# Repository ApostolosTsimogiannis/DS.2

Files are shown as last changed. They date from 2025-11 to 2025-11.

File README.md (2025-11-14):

# DS.2 RC Helicopter
DS.2 is a mostly printable 570 size RC helicopter for acrobatic and 3D flight.

All files are downloadable for users to build this heli. Read the manual section for a complete build instruction.
<br>

> This repository is under development. The final sections of the manual are being written and some more part files will be added.
<br>

manual

# Technical Specifications:

|Description|Value|
|---|---|
| Length | 1120mm |
| Height | 355mm |
|Width (skids)|  190mm|
|Weight (no battery)| 2180kg (1)|
|Motor Size| 4020-4025|
|Servos| Both 15mm and 20mm servos can be used|
|Main blade Size| 560-600mm (2)|
|Tail blade size| 85-95mm (2)|
|Battery|6s 4000-5600mAh|

(1) With 15mm servos

(2) Depending on tail belt length.
<br>
<br>

> ## Licensing:
> This work is licensed under Creative Commons Attribution-NonCommercial-ShareAlike 4.0 International.
To view a copy of this license, visit https://creativecommons.org/licenses/by-nc-sa/4.0/
<br>

> ## Disclaimer:
> Remote Control (RC) Helicopters can cause harm or death to people and animals and damage to property. By following the information shared in this repository, downloading the part files, and building the helicopters, or using the parts in other ways, the user agrees that all responsibility lies with them. The designer is not liable for any harm or damages arising from the use or these parts and cannot guarantee in any way the operation of the components or the helicopter as a whole. Using the parts, assembling the helicopter and using it, is at the users own risk and they hold all resposnibility and liability. Operate all RC vehicles in accordance with safety guidelines and local law requirements.
<br>

## Information/Social:
- https://www.youtube.com/@apostolosnt
- https://www.facebook.com/ds.x.rc.heli.project
- https://grabcad.com/a.t-79

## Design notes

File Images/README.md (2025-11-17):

Renders and other images of the DS.2.






1735820079988s

1744195786972s

DS 2 v2 1 front 2

DS 2 v2 1 front 3

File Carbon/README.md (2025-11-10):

All carbon parts are included in this folder.

Sheet parts are STEP files with a PDF basic drawing to ensure no issues with scaling.

The tail tube is a 25mm diameter, 680mm length tube. Tube thickness 1mm. It is strongly recommended that the inside of the carbon tube is sprayed with some varnish to stop the carbon dust from coming of with the belt.

The tail control rod is a 4mm diameter tube, 660mm length. This will be cut to size according to the type of ball links and the length of the 2.5mm thread used. See more details in the manual.

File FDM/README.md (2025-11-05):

- All parts in this folder are intended for FDM printing on your personnal 3D printer. These can be printed in SLS/MJF as well. No nested file of all parts has been created.
- Some parts e.g. canopy, are cut into appropriate sections for personal 3D printers.
- Material can be PLA, PETG or other.
- Refer to the manual section for part quantites to complete the build.

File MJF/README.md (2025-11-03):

All parts in this folder are intended for MJF printing. SLS is also suitable.

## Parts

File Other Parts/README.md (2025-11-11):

This section includes other parts that are optional. For example ESC mounting plates etc. You can choose which manufacturing method you will use for these.

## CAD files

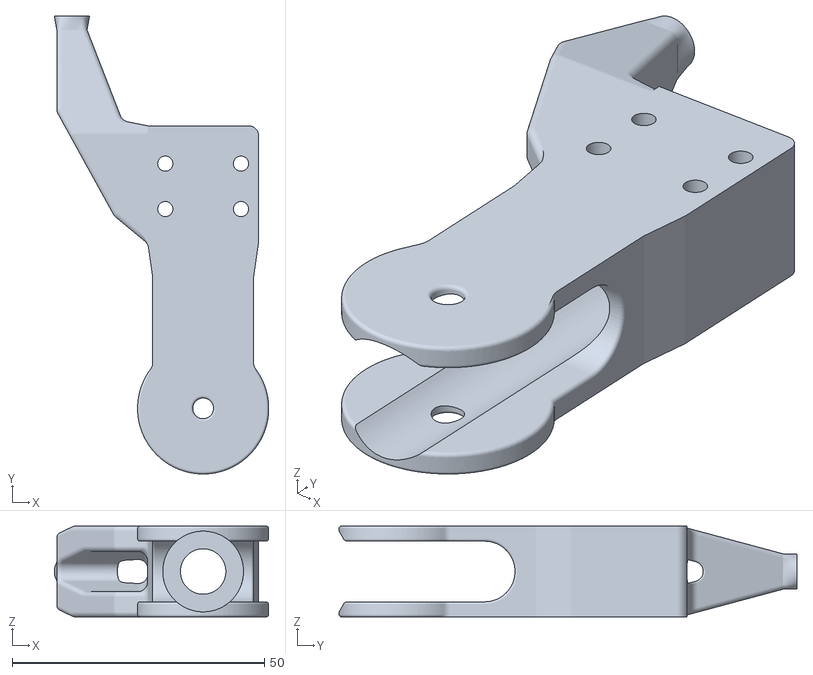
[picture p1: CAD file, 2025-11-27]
MJF/02-033-20 main grip.STL
42.5 x 90.8 x 18.0

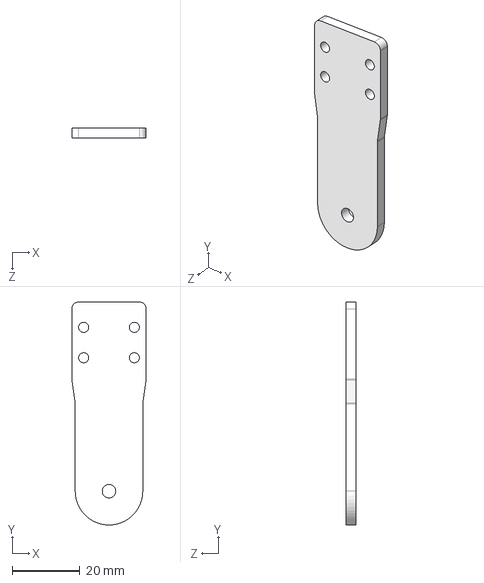
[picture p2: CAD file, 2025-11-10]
Carbon/02-014-20 main grip plate.STEP
22.0 x 66.0 x 3.00 mm

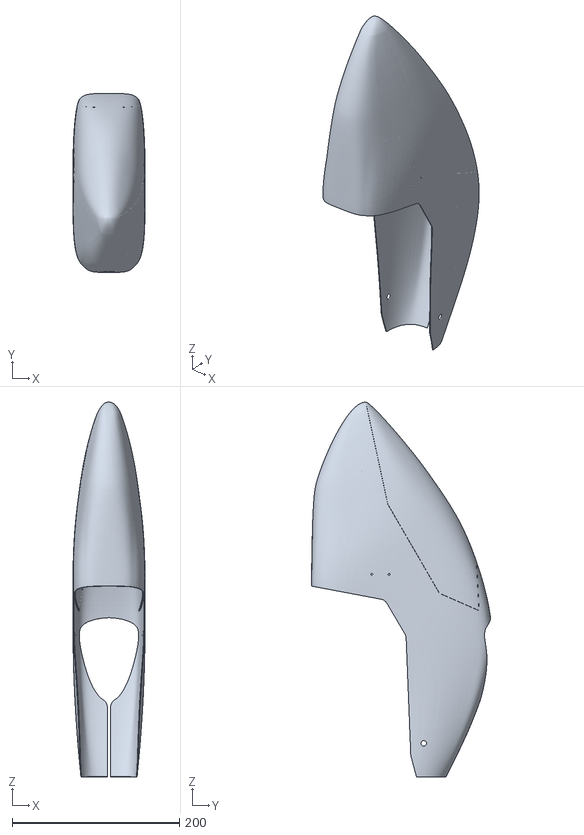
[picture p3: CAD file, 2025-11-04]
FDM/DS2 canopy assembly 0.90mm.STL
86.0 x 213.9 x 447.9

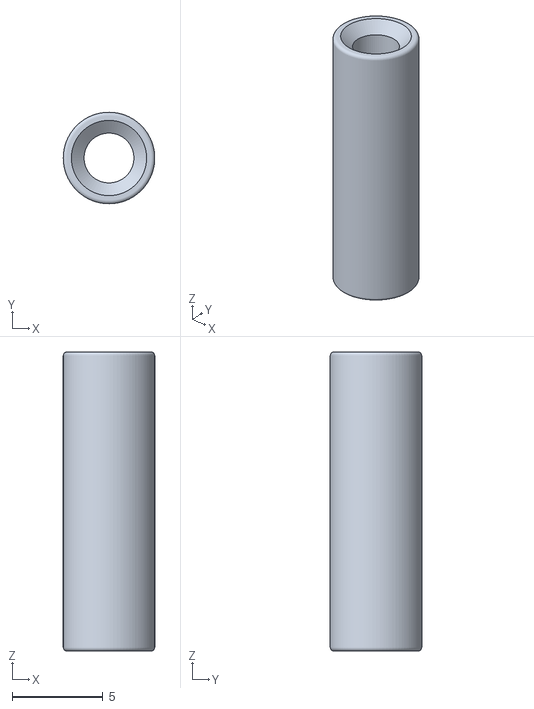
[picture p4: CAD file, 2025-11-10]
MJF/02-048-10 main grip link tube.STL
5.05 x 5.05 x 16.5

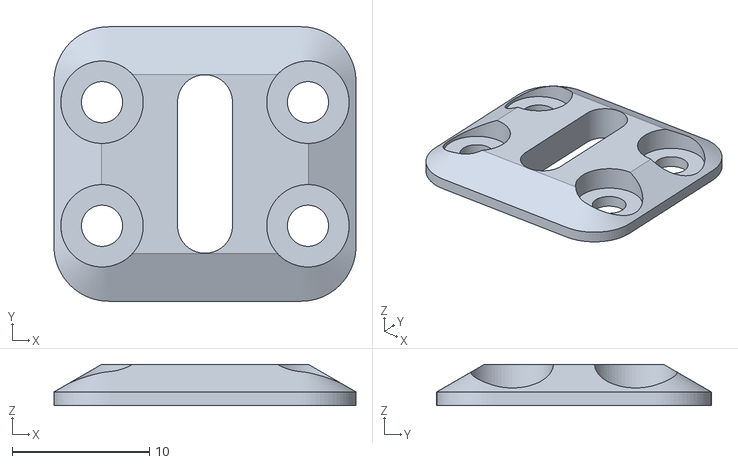
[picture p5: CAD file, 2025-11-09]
MJF/02-037-10 main grip top.STL
22.0 x 20.0 x 3.00

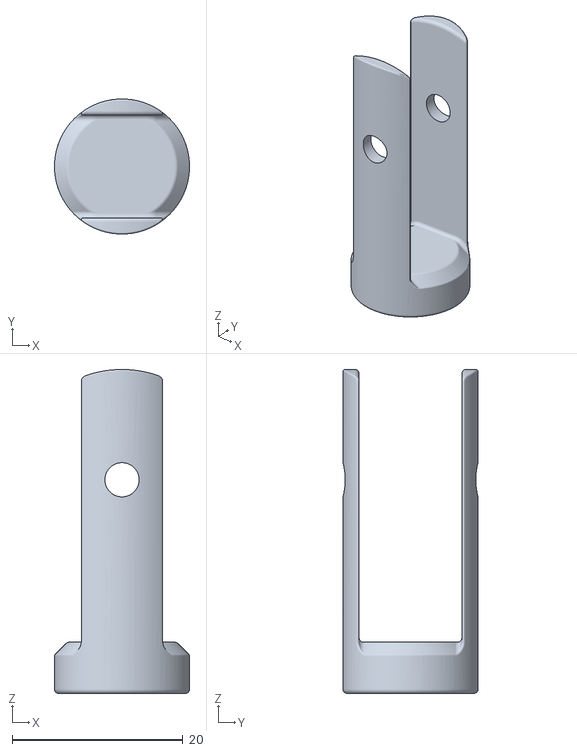
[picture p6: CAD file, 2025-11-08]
MJF/02-075-10 main grip insert.STL
15.8 x 15.8 x 37.9

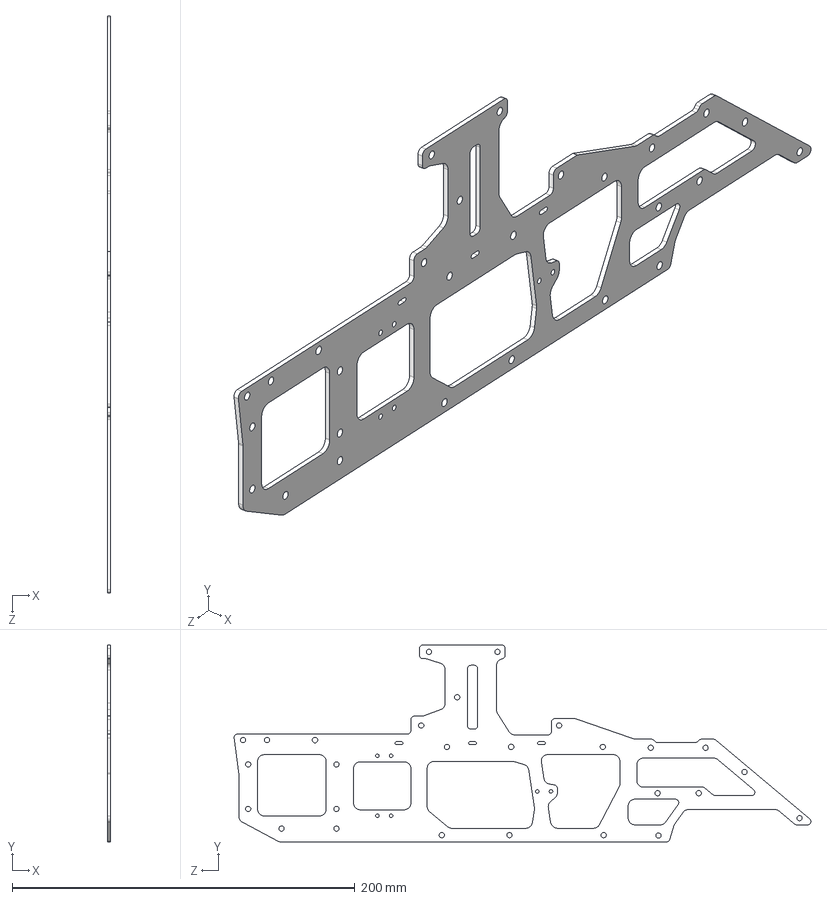
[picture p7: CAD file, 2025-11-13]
Carbon/02-010-21 side plate Right.STEP
2.00 x 115.0 x 336.7 mm

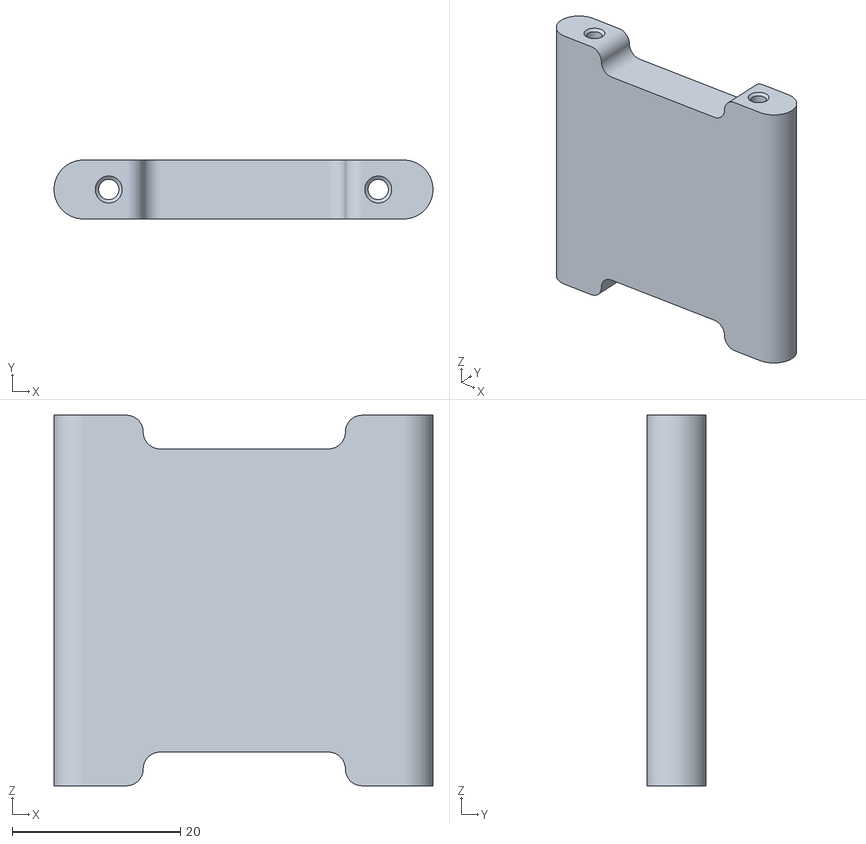
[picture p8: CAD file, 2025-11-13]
FDM/02-031-10 rear lower tray.STL
45.0 x 7.00 x 44.0

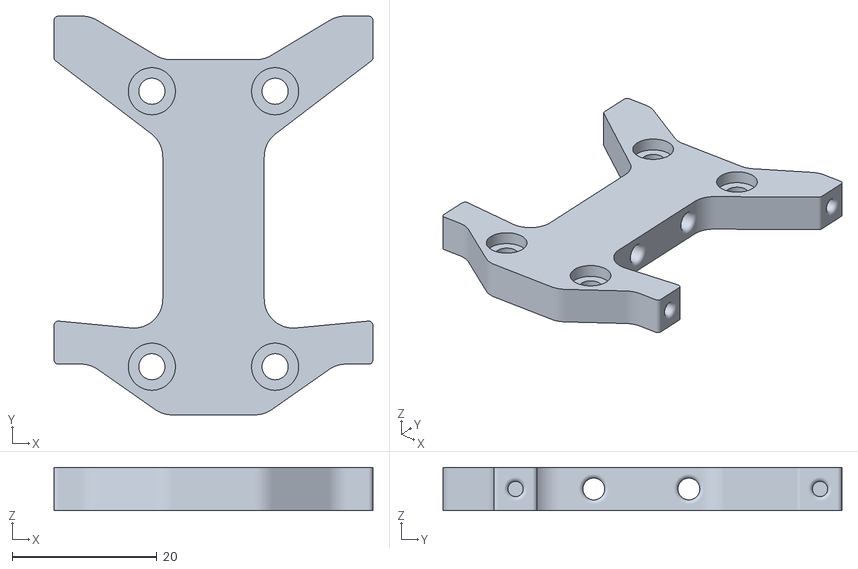
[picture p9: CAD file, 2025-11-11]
Other Parts/HW 150 mount for DS2.STL
44.0 x 55.0 x 6.00

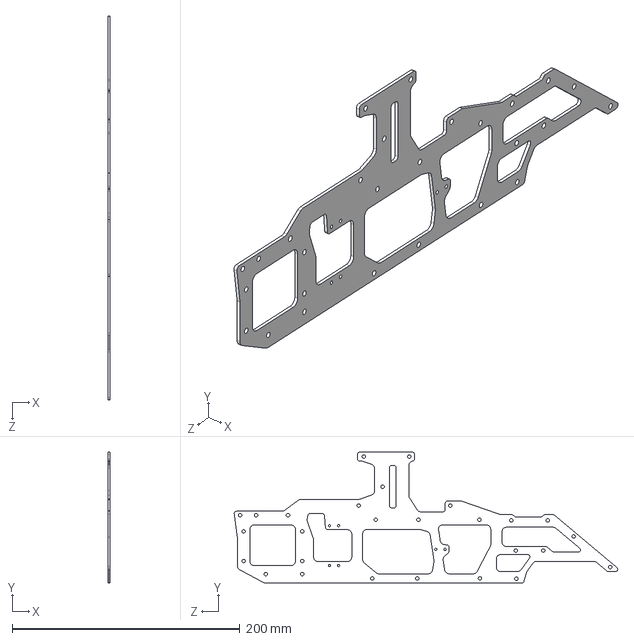
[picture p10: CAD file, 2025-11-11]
Carbon/02-010-21 side plate Left.STEP
2.00 x 115.0 x 336.7 mm

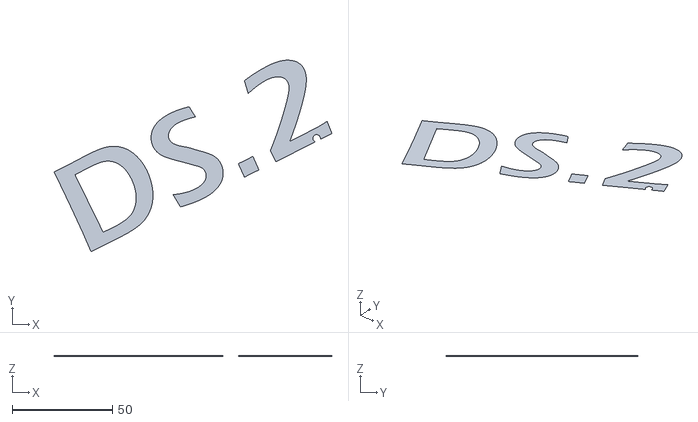
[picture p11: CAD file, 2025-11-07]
FDM/DS2 canopy logo only 0.3mm.STL
138.4 x 95.4 x 0.3

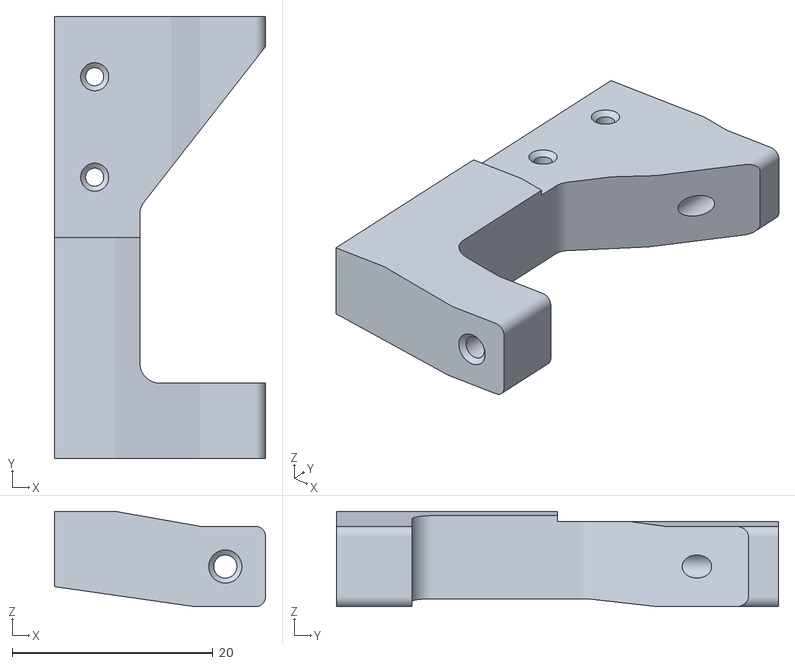
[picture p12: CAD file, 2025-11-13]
MJF/02-065-10 rear servo support for 20mm servo.STL
21.0 x 44.0 x 9.50

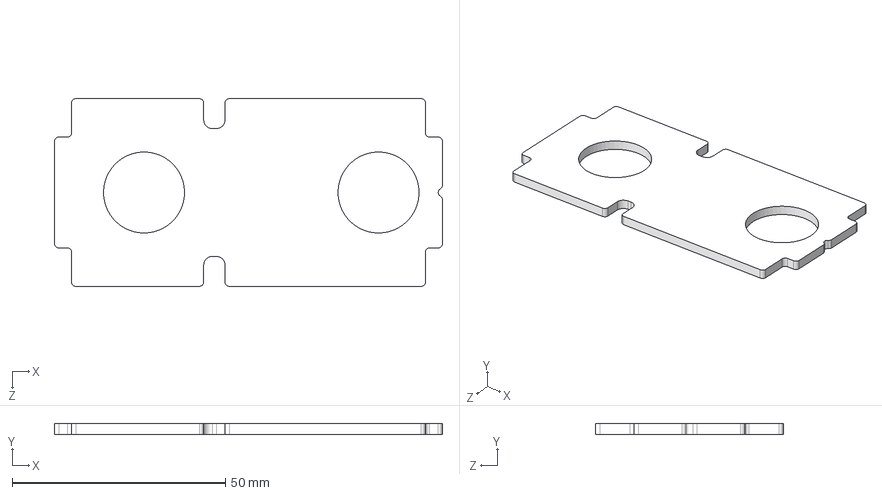
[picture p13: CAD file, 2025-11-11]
Carbon/02-008-21 middle plate.STEP
91.0 x 2.50 x 44.0 mm

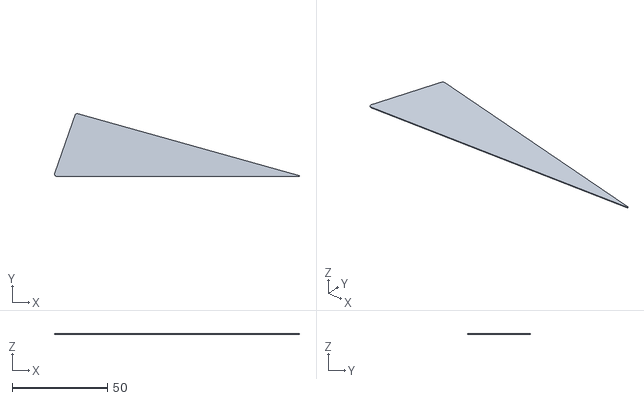
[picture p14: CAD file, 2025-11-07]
FDM/triangle 0.3mm.STL
128.7 x 33.0 x 0.3

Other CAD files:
MJF/02-037-10 main grip top hex.STL
MJF/02-064-10 front servo support for 20mm servo.STL
Carbon/02-007-21 lower plate.STEP
FDM/DS2 canopy logo only 0.3mm inverted.STL
Carbon/02-007-21 lower plate.STL
Carbon/02-008-21 middle plate.STL
Carbon/02-009-20 top plate.STEP
Carbon/02-009-20 top plate.STL
Carbon/02-010-21 side plate Left.STL
Carbon/02-010-21 side plate Right.STL
Carbon/02-011-10 rear bow support.STEP
Carbon/02-011-10 rear bow support.STL
Carbon/02-012-10 front bow support.STEP
Carbon/02-012-10 front bow support.STL
Carbon/02-013-10 head plate.STEP
Carbon/02-013-10 head plate.STL
Carbon/02-014-20 main grip plate.STL
Carbon/02-015-10 tail fin.STEP
Carbon/02-015-10 tail fin.STL
FDM/02-016-10 front landing bow.STL
FDM/02-017-10 rear landing bow.STL
FDM/02-018-10 landing skid Left.STL
FDM/02-018-10 landing skid Right.STL
FDM/02-023-10 front canopy support Left.STL
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

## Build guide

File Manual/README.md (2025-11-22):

# DS.2 RC Helicopter Build Manual

## Introduction:

The DS.2 is the second helicopter of the DS.X RC Heli Project. The helicopter was designed with the flowing goals: 
- Make a fully 3D capable RC helicopter.
- The helicopter must be in the 550 to 600 class.
- Be as light as possible.
- Use the minimum number of metallic parts.
- Be 3D printable.
- Use as many parts as possible that are available on the market (not helicopter specific).
- Be able to use parts from multiple other helicopter brands where needed (metallic parts).

These would make the helicopter essentially an ‘open source’ type of project since builders can make the parts locally and cheaply. The very low count of metallic parts guarantees that this helicopter will never run out of spares either!

The design started in December 2023 and settled to a 570 size and was completed in 2024. It has flown very well and has proven reliable and robust in moderate 3D flight, including a few crashes!
A few parts underwent small modifications and this is the final version (v2.1) of the helicopter. 

Since each build will be unique, _each builder must treat this as a prototype helicopter_.

Enjoy the build!

*Apostolos Tsimogiannis*

If you want to ask anything contact me at:
apostolos.tsimogiannis@gmail.com 

or send a friend request to “DS.X RC Heli Project” on FB and message me.

You can see videos of the DS.2 and other projects at https://www.youtube.com/@apostolosnt.

<br>
<br>

> ## Licensing:
> This work is licensed under Creative Commons Attribution-NonCommercial-ShareAlike 4.0 International.
To view a copy of this license, visit https://creativecommons.org/licenses/by-nc-sa/4.0/
<br>

> ## Disclaimer:
> Remote Control (RC) Helicopters can cause harm or death to people and animals and damage to property. By following the information shared in this repository, downloading the part files, and building the helicopters, or using the parts in other ways, the user agrees that all responsibility lies with them. The designer is not liable for any harm or damages arising from the use or these parts and cannot guarantee in any way the operation of the components or the helicopter as a whole. Using the parts, assembling the helicopter and using it, is at the users own risk and they hold all resposnibility and liability. Operate all RC vehicles in accordance with safety guidelines and local law requirements.
<br>

## General information about the build:

The DS.2 is a RC helicopter intended for hobbyists with advanced knowledge of assembling helicopters and tool skills to build or adapt parts. This manual is not an exhaustive presentation of the build process and good assembly practices and knowledge of RC helicopter assembly are prerequisites for this build.

The builder must be capable and have the tools to:

- Drill precision holes in hardened steel shafts.
- Cut hardened shafts.
- Use drills or other tools to drill or clean holes and bearing seats.

The model is built using the following materials:
- Carbon sheet.
- MJF (MultiJet Fusion) 3D printed parts.
- FDM 3D printed parts (no specific material is required).
- Existing parts of commercially available RC helicopters.
- Bearings, screws, belts and other widely available on the market.

Materials and tools are required:
- Thread lock.
- Epoxy glue.
- Lubricating oil/grease.
- Soldering iron.
- Hex, torx and other drivers, depending on the screws used.

Some of the parts needed are from common RC helicotpter models available on the market, such as Mikado Logo 600 series, Goosky RS5 or RS6, Align etc., so these parts may already be available to the builder from other projects.
All parts, except from the shafts (main, spindle, 1st Stage, tail, tail spindle) can be found on the market. It is recommended the shafts are bought from existing models unless the builder has access to machining and case hardening.

<ins>Use thread locking compound in all metal to metal contacts except when a lock nut is used.</ins>

For metal thread screws into MJF plastics, thread locker is not needed but the thread forming must not go through the entire thread depth. Allow some length for the screw to cut its own thread and ‘lock’ with the mating MJF piece. Be careful of how much you tighten such screws. 
Regardless of where a bolt threads into, remember you are tightening M2, M2.5, M3 screws. Do not treat them like M30!

All metal thread bolts used must be high strength.

When using screws specifically made for plastic, no thread tool is needed. The screw will form its own thread and can be tightened more than metal screws in plastic. These screws are not very good at being removable and over-tightening them will reduce further the number of times they can be loosened and tightened.

All bearing seats must be cleaned with a tool that has a square edge. Some screwdrivers will do, or square tip exacto knives. The seat must be cleaned form the nylon powder and the edges pressed. This will make the bearing seat better. All nylon parts have a small surface roughness which allows for some give, so bearings fit with a moderate transition fit, perfect for the use.

MJF 3D printed parts are only accurate to 0.1mm (or less) which is not machining accuracy, therefore some part assembly may require part cleaning. The work on the pieces should not require material removal and parts should fit as expected. If this is not the case then discuss with your MJF parts manufacturer.

It is recommended that SLS is not used as a process. Depending on the implementation parts may be more brittle that expected. Discuss with your 3D print shop and maybe test one or two pieces for flexibility.
<br>
<br>

## Mechanical Parts Needed:
<details> 
  
<summary> Open Chapter </summary>

|Description|Qty|Use|Remarks|
|---|---|---|---|
|8x16x5 bearing|	4|	Grip	| |
|8x16x5 thrust bearing|	2|	Grip	|F8-16M|
|10x19x5 flanged bearing|	5| Main and Stage 1| shaft	|F6800-ZZ|
|6x13x5 bearing|	1|	Motor support	| |
|3x7x3 bearing|	10|	Tail belt guides, tail arm, stage 1 belt idler, stage 2 belt idler|	683ZZ|
|5x13x4 flanged bearing|	2|	Tail case for 5mm tail shaft|	F695|
|6x10x2.5 bearing|	2|	Tail slider|	MR106 W2.5|
|4x8x3 bearing|	2|	Tail grip|	MR84ZZ|
|4x8x3.5 thrust|	2|	Tail grip|	F4x8S|
|4x8x2 bearing|	2|	Tail grip|	MR84|
|Belt 3M 234mm/10mm (L/W)|	1|	Stage 1 belt|	STD and HTD belts can be used. Prefer STD (e.g. S3M) belts. With HTD belts there will be somewhat higher friction and reduced service life.|
|Belt 3M 234mm/15mm (L/W)|	1|	Stage 2| belt|	STD and HTD belts can be used. Prefer STD (e.g. S3M) belts. With HTD belts there will be somewhat higher friction and reduced service life.|
|Belt 3M 1680-1698mm/6mm| 	1|	Tail belt|	Use any length in this range. Adjust tail boom length accordingly. 1680mm is max 560mm main blade and 85mm tail blades. 1698 allows up to 600mm main and 95mm tail blades. Check blade interference when before flight. Suitable belts from helis are Goblin 570, Goosky RS5. |
|  |  |  |  |			
|Washer 4x8x0.5|	>4|	Tail| |
|Washer 3x7x0.5|	>4|	Idlers (if needed)| |
|Washer 8x12x0.5|	2|	Head| |
|Washer 10x16x0.5, 0.2|	>8|	Head, main shaft, stage 1 shaft| |
| | | | |
|2.9x6mm for plastic|	>4|	Frame	| |
|2.9x8mm for plastic|	40|	Frame	| |
|2.9x10mm for plastic|	>10|	Frame	| |
|2.2x6mm for plastic|	2|	Locating screws for tail boom	| |
|2.2x10mm for plastic|	16|	Servos	|Or servo screws |
| | | | |
|M2x8|	10|	Belt idler supports	| |
|M3x12|	8|	Motor plate, landing bows	| |
|M3x16|	6|	Grips, tail, frame	| |
|M3x20|	7|	Tail grips, idlers	| |
|M3x25|	7|	Head, tail, idlers	| |
|M3x30|	12|	Grips, tail, head	| |
|M4 x 30|	2	|Grips	| |
|  |  |  |  |		
|Stage 1 shaft, 10mm dia, 57mm length|	1|	Stage 1 shaft|	See drawing for hole position and size.|
|Main shaft, 10mm dia, 184mm length|	1|	Main shaft|	See drawing for hole positions and size.|
Spindle, 8mm dia, 108mm length|	1|	Spindle	Mikado Logo 600 compatible.| Adaptations to fit other spindles is possible but depending on length the helicopter response and flying characteristics will change.|
|Tail shaft and spindle|	1|	Tail|	Tail shafts and the corresponding spindles that can be used: Mikado Logo 600/550 series,	Goosky RS5, other models will fit as long as they are 5mm or 6mm diameter. Some modification to the control mechanism may be required to get the required CW/CCW throws.|
|Tail bronze slider| 1| Tail| This must be from the corresponding tail used i.e. for 5mm or 6mm shaft.|
|Swash|	1|	Head|	Any swash that is designed for a 10mm shaft can be used. The original design head geometry requires the two front ball links to be 62mm to 63mm center distance. Using any swash in the market, a set of ball links can be found to fit this requirement. Other distance will alter the linearity of the head.			Swash plate from Align, Mikado, Steam etc will work. See more details further in the manual.|
|One Way Bearing (OWB) and Hub|	1|	Main shaft transmission|	A suitable main shaft OWB is required. The main pulley is designed for the Mikado Logo 600 OWB and hub but it can be adapted to other hubs in the market. The file is in STEP format so it can be adapted. With users adapting it to other hubs the file download will be expanded to include parts ready to accept other OWB hubs.|
|17T 3M motor pulley|	1|	Stage 1 transmission|	An alu pulley is needed at the motor. These are readily available on the market (usually AF type for 10mm belt).|
|Dowel pins 3mm|	3|	Tail belt tensioners|	2x19mm, 1x28mm|
|Dowel pins 2mm|	1|	Tail pulley	|

</details>
<br>
<br>

## Manufactured Parts:
<details>
<summary> Open Chapter </summary>

|Part ID|Part Name|Process/Material|Quantity|
|---|---|---|---|
|02-001-10|front shaft|CNC hardened steel|1|
|02-002-10|main shaft|CNC hardened steel|1|
|02-003-20|3M 56T Stage 1 pulley|MJF/SLS nylon|1|
|02-004-10|3M 22T|MJF/SLS nylon|1|
|02-005-10|3M 67T|MJF/SLS nylon|1|
|02-006-10|3M 56T OWB pulley|MJF/SLS nylon|1|
|02-007-21|lower plate|3K carbon sheet 2.5mm|1|
|02-008-21|middle plate|3K carbon sheet 2.5mm|1|
|02-009-20|top plate|3K carbon sheet 2.5mm|1|
|02-010-21|side plate (Right and Left editions)|3K carbon sheet 2.0mm|2|
|02-011-10|rear bow support|3K carbon sheet 2.0mm|2|
|02-012-10|front bow support|3K carbon sheet 2.0mm|2|
|02-013-10|head plate|3K carbon sheet 2.5mm|2|
|02-014-20|main grip plate|3K carbon sheet 3.0mm|4|
|02-015-10|tail fin|3K carbon sheet 2.0mm|1|
|02-016-10|front landing bow|FDM, PLA/PETG/other|1|
|02-017-10|rear landing bow|FDM, PLA/PETG/other|1|
|02-018-10|landing skid (Right and Left editions)|FDM, PLA/PETG/other|2|
|02-019-10|motor plate|MJF/SLS nylon|1|
|02-020-10|lower motor plate|MJF/SLS nylon|1|
|02-021-10|front battery mount|MJF/SLS nylon|1|
|02-022-20|rear battery mount|MJF/SLS nylon|1|
|02-023-10|front canopy support (Right and Left editions)|FDM, PLA/PETG/other|2|
|02-024-10|rear canopy support (Right and Left editions)|FDM, PLA/PETG/other|2|
|02-025-20|frame cross member|MJF/SLS nylon|3|
|02-026-10|top plate front suppport for 15mm servo|MJF/SLS nylon|1|
|02-027-10|top plate rear suppport for 15mm servo|MJF/SLS nylon|1|
|02-028-10|front servo suppport for 15mm servo|MJF/SLS nylon|1|
|02-029-10|rear servo support for 15mm servo|MJF/SLS nylon|1|
|02-030-10|rear tray servo mount for 15mm servo|MJF/SLS nylon or FDM PLA/PETG/other|1|
|02-031-10|rear lower tray|FDM, PLA/PETG/other|1|
|02-032-20|head block damped|MJF/SLS nylon|1|
|02-033-20|main grip|MJF/SLS nylon|2|
|02-034-20|frame lateral member|MJF/SLS nylon|1|
|02-035-10|carbon plate single support|MJF/SLS nylon|4|
|02-036-20|fixed swash driver|MJF/SLS nylon|2|
|02-037-10|main grip top|MJF/SLS nylon or FDM PLA/PETG/other|4|
|02-038-10|tail belt roller|MJF/SLS nylon|2|
|02-039-10|tail belt roller support|MJF/SLS nylon|2|
|02-040-10|tail belt arm support|MJF/SLS nylon|1|
|02-041-10|tail belt arm support bottom|MJF/SLS nylon|1|
|02-042-10|tail belt tensioner arm|MJF/SLS nylon|1|
|02-043-10|tail belt spring support|MJF/SLS nylon|1|
|02-044-10|tail boom bracket|MJF/SLS nylon|2|
|02-045-20|1st stage roller|MJF/SLS nylon|1|
|02-046-10|2nd stage roller|MJF/SLS nylon|1|
|02-047-10|stage 2 roller support|MJF/SLS nylon|1|
|02-048-10|main grip link tube|MJF/SLS nylon|2|
|02-049-10|tail rod guide|MJF/SLS nylon or FDM PLA/PETG/other|1|
|02-050-20|tail case|MJF/SLS nylon|1|
|02-051-10|3M-15T tail pulley|MJF/SLS nylon|1|
|02-052-10|tail arm|MJF/SLS nylon|1|
|02-053-10|tail control housing|MJF/SLS nylon|1|
|02-054-10|tail control fork|MJF/SLS nylon|1|
|02-055-10|tail link|MJF/SLS nylon|2|
|02-056-10|tail grip|MJF/SLS nylon|2|
|02-057-10|head damper|FDM, TPU80|2|
|02-058-10|tail control fork 6mm shaft|MJF/SLS nylon|1|
|02-059-10|tail control housing 6mm shaft|MJF/SLS nylon|1|
|02-060-10|tail arm 6mm shaft|MJF/SLS nylon|1|
|02-061-10|tail damper|FDM, TPU80|2|
|02-062-10|top plate front support for 20mm servo|MJF/SLS nylon|1|
|02-063-10|top plate rear support for 20mm servo|MJF/SLS nylon|1|
|02-064-10|front servo support for 20mm servo|MJF/SLS nylon|1|
|02-065-10|rear servo support for 20mm servo|MJF/SLS nylon|1|
|02-066-10|rear tray servo mount for 20mm servo angled|MJF/SLS nylon|1|
|02-067-10|rear tray servo mount for 20mm servo|MJF/SLS nylon or FDM PLA/PETG/other|1|
|02-068-10|rear servo support for 15mm head 20mm tail servo|MJF/SLS nylon or FDM PLA/PETG/other|1|
|02-069-10|front cable channel|FDM, PLA/PETG/other|1|
|02-070-10|canopy|FDM, PLA/PETG/other|1|
|02-071-10|canopy support|FDM, PLA/PETG/other|2|
|02-072-10|tail boom 680x25mm|Carbon tube|1|
|02-073-10|tail control rod 660x4mm|Carbon tube|1|
|02-074-10|2nd stage roller insert|FDM, PLA/PETG/other|1|
|02-075-10|main grip insert|MJF/SLS nylon|2|
|02-079-10|tail grip for 6mm tail shaft|MJF/SLS nylon|2|
|02-080-10|3M-14T tail pulley for 6mm shaft|MJF/SLS nylon|1|
|02-081-10|tail boom bracket w insert (full and plain editions)|MJF/SLS nylon|1|
|02-082-10|tail boom bracket insert|MJF/SLS nylon|1|

</details>
<br>

## Making the Main and Stage 1 Shafts:
<details> 
<summary> Open Chapter </summary>

The main shaft can be manufactured from a variety of shafts on the market. Mikado 199mm shaft is convenient as it has the top hole at approx. the right position. The 1st stage shaft can be made from any 10mm shaft on the market. <br>
Since the shafts are hardened, it is recommended that the position of the drilling for the holes is lightly flattened with a Dremel disk so the case hardening is removed and it becomes easier to drill. Use a low speed drill. <br>
Some dimensions do not need to be exactly as shown below. Shaft length can vary up to +2mm. Hole positioning can be within 1mm or more of the shown dimension, but consider the following: <br>
The relative distance between the two holes on the Stage 1 shaft needs to be accurate for parts to fit, and for links to have the dimensions shown in this manual, the relative distance between the two holes on the main shaft needs to be accurate. 
<br>
NOTE: drilled holes are shown as 3.1mm. The drill bit used can be 3.0mm since M3 bolts are slightly below this value.



</details>
<br>

## Stage 1 Shaft Assembly:
<details> 
<summary> Open Chapter </summary>

### Preparation:
Use a 10mm diameter drill bit to clean out the shaft hole of the printed pulleys. Do not use a normal high speed drill. If you do not have a low speed drill press, use a choke and drill bit, and drive it through by hand, turning as you go. Go back and forth s few times to clean out any surface debris form the printing process and smooth out any inacuracies.
Use the 2nd M3 thread tool to tap the smaller diameter hole side. This is were the positioning bolt will thread into. <br>
Assemble as shown below.



</details>
<br>

## Main Shaft and Stage 2 Assembly:
<details> 
<summary> Open Chapter </summary>

### Preparation:
Clean all surfaces and the 10mm shaft hole of the tail pulley as in the previous section. <br><br>
Assemble as shown below.<br>
Use 2 10x0.5mm washers between the OWB and the tail pulley.<br>
For a Mikado OWB hub (shown below) use 5 10x0.5mm washers below the OWB.<br>
Use 1 10x0.5mm washer above the tail pulley.<br>



</details>
<br>

## Lower Plate Assembly:
<details> 
<summary> Open Chapter </summary>

### Preparation:
Clean all surfaces of the 3D printed parts with a small screwdriver. Make sure there is no nylon powder residue on the surface. You can use an air gun if you have one.<br>
Prepare a small amount of two-part epoxy.
<br> <br>
Use epoxy on all areas marked with the orange arrow in the drawing. Make sure you do not use too much and it overspills as it will require more cleaning later. Especially the bearings need a very small amount only, to function as a retainer. CA glue can also be used for the bearings. Press the 3D printed parts onto the carbon plate so they are flush with the edges and do not protrude. This is important for the fit in the assembled frame later.<br>
The 4 screws are plastic-specific screws 2.9x6mm. If you cannot find self tapping flat tip ones, and you use pointed screws it’s suggested you cut the tip and do not allow it to protrude.



</details>
<br>

## Mid Plate Assembly:
<details> 
<summary> Open Chapter </summary>

### Preparation:
Clean all surfaces of the 3D printed parts with a small screwdriver. Make sure there is no nylon powder residue on the surface. You can use an air gun if you have one.<br>
Prepare a small amount of two-part epoxy. <br><br>
Use epoxy on all areas marked with the orange arrow in the drawing. Make sure you do not use too much. Especially the bearings need a small amount only, to function as a retainer. CA glue can also be used for the bearings. Press the 3D printed parts onto the carbon plate so they are flush with the edges and do not protrude. This is important for the fit in the assembled frame later.



</details>
<br>

## Top Plate Assembly:
<details> 
<summary> Open Chapter </summary>
### Preparation:
Clean all surfaces of the 3D printed parts with a small screwdriver. Make sure there is no nylon powder residue on the surface. You can use an air gun if you have one.<br>
Prepare a small amount of two-part epoxy for the bearing only. In this instance the 3D printed parts are fitted without glue so they can easily be replaced. <br><br>
Use epoxy at the areas marked with the orange arrow in the drawing. Make sure you do not use too much and it overspills. Especially the bearings need a small amount only, to function as a retainer. CA glue can also be used for the bearings. <br> <br>



</details>
<br>

## Main Grip Assembly:
<details> 
<summary> Open Chapter </summary>

### Preparation:

Clean the bearings seats inside the grip with a small screwdriver and a square tip tool. Make sure there is no nylon powder residue on the surface and especially in the bearing seat.
Tap the grip arm ball link bolt hole with M3 tap tool. Do not bottom out the tool. Clean the four M3 holes and make sure the M3x30 bolts go through.
<br>
<br>
Per grip you will need:<br>
1x M3x16<br>
1x M3 washer<br>
4x M3x30<br>
4x M3 lock nuts<br>
1x M4x35<br>
1x M4 lock  nut <br>
2x 8x16x5 bearings<br>
1x 8x16x5 thrust bearing<br>
1x Ø10 washer (0.5, 0.2, 0.1 as needed)<br>
1x 8x0.5 washer<br>
<br>
Grease the thrust bearing as needed and position it with the small diameter to the outside.
<br>

Use the inner Ø10 washers as needed to allow
minimal play of each grip when assembled (~0.2mm max total gap).

The Ø8 washer must only contact the inner race of the outer bearing.

You can leave the ball link for later, as you need to add the grip arm link
before you insert the bolt into the grip (highlighted in the drawing).
The grip arm ball link can be from any helicopter as long as it fits an M3 bolt.
Mikado grip-arm ball links work well.



</details>
<br>

## Head Assembly:
<details> 
<summary> Open Chapter </summary>

## Damped Head:<br>

### Preparation:<br>

Clean all 3D printed parts of any nylon powder residue on the surface and especially in the damper seat.<br>
Make sure all M3 bolts can pass through the main head block.<br>

You will need:<br>
6x M3x25<br>
6x M3 lock nuts<br>

Assemble the main head block with the dampers and the spindle first.<br>



## Undamped Head:

The assembly and preparation are identical. There are just no dampers! See notes regarding FBL gains etc in the final assembly section.

</details>
<br>

## Tail Grip Assembly:
<details> 
<summary> Open Chapter </summary>

### Preparation:

Clean the bearings seats inside the grip with a small screwdriver and/or a square tip tool. Make sure there is no nylon powder residue on the surface and especially in the bearing seat.

Tap the grip arm ball link bolt hole with M2.5 tap tool. Do not bottom out the tool.

Per grip you will need:<br>
1x M2.5x10<br>
1x M2.5x6<br>
1x M2.5 washer<br>
1x 4x8x3 bearing<br>
1x 4x8x2 bearing<br>
1x 4x8x3.5 thrust bearing<br>
1x 4x8x0.5 washer<br>

Grease the thrust bearing as needed and position it with the small diameter to the outside.



</details>
<br>

## Tail Spindle-Shaft Assembly:

<details> 
<summary> Open Chapter </summary>

## Damped:

### Preparation:

When using the Goosky RS5 tail parts, drill a 2.1mm hole at the center of the flats on the shaft.

Use the TPU printed dampers.

Assemble as shown. 



## Undamped:

Assemble parts using thread lock for the set screw. The example below is with Mikado 550/600 tail parts.



</details>
<br>

## Motor Assembly:
<details> 
<summary> Open Chapter </summary>

### Preparation:

Clean the bearings seat of the lower plate with a small screwdriver and/or a square tip tool. Make sure there is no nylon powder residue on the surface.

To mount the motor plates to the frame screws for plastic or bolts can be used. 
If using bolts, the holes must be tapped. Tap the 4x M3 holes of the top plate and the 4x M2.5 on the lower plate. Do not tap all the way through so the last few threads lock into the plastic.

Also tap the 1x M3 position on the lower frame, where the tensioner roller bolt will thread into.

Assemble the motor on the motor plates. The motor plate hole pattern is 2x M4 Ø25mm and 2x M4 Ø30mm.<br>
1x 6x13x5 bearing.<br>
2x M4x10 bolts (or other depending on the motor used).<br>
1x 3M 17T pulley. <br>



</details>
<br>

## Main Frame Assembly:
<details> 
<summary> Open Chapter </summary>

Assemble all parts as shown below. It is important to get all belts on at this stage.

Use 5x 0.5mm Ø10 washers under the OWB if using a Mikado 600 OWB hub and one above the tail pulley.

Add one 0.5mm Ø10 washer at the top and bottom of the Stage 1 shaft.


<br>
<br>

Assemble the side frames as shown below.
Use screws for plastic in all MJF parts 2.9x8 and 2.9x10 are needed. 
Assemble both side frames to check any vetical play of the main and stage 1 shafts. Add or remove washers as needed to make sure the shaft is not compressed between the plates and that there is no play. Also check that the OWB pulley is not sitting too low and touches the frame.
<br>
The front battery support must be tapped M3. See lower frame assembly.
<br>



<br>
<br>

Once the shafts are fitted, other parts can be fitted like the motor and tail belt guide pulleys and all the servo supports. 
<br>
<br>
The choice of plate/servo supports depends on the servo set used. Refer to the part list to identify parts numbers for 15mm, 20mm and mixed 15-20mm setups. 
<br>
<br>
The tail belt guide pulley assemblies can be removed and replaced at any point since they are easy to get to.
<br>
These are assembled using M2 bolts or 2mm screws for plastic.


<br>
<br>

Add remaining compenets as shown below.
For the tail boom support brackets, there are options how to set them up. A single tighening bracket can be used along with a plain one (shown below) or two tightening brackets can be used.
The top piece needs threads cut into it where the M3x25 will thread into.
All parts assembled with screws for plastic.

A locating screw must be added on the underside of the rear bracket.
This will be done later, after the tail has been assembled and the tail belt tensioned.
<br>



Use screws for plastic where the screws go into MJF parts. 
<br>
The landibng bows are designed for M3 thread inserts. Use 5.7mm length M3 inserts and M3x10 or M3x12. 
Use thread locking compound.
<br>
<br>



<br>
<br>


<br>
<br>


<br>
<br>


</details>
<br>

## Tail Assembly:
<details> 
<summary> Open Chapter </summary>

### Preparation:

Clean the bearings seat of the housing with a small screwdriver and/or a square tip tool. Make sure there is no nylon powder residue on the surface.
Clean the surface of the two links and the fork to make sure there is no roughness from the printing process that will prevent them from moving completely free and smooth between them.
Do not overtighten the M3 and the two M2 bolts. Make sure after assembly that everything runs absolutely smooth and free.
<br>
The holes on the arm are for M2 ball links. You do not need to tap the holes. Threading the ball link directly will cut its own thread and provide a good lock. If you do tap it, only tap the first few theards.
<br>
Fitting the control fork onto the bronze slider is a tricky part of the assembly. If you have the correct tapping tool (M7 or M8, depending on the shaft diameter) make a start to the thread without going all the way through so the fork will lock in the last few threards.
This can also be done by simply carefully threading the fork onto the slider and let it cut the threads. You need to be extra careful since the larger diameter of the slider with short thread pitch can easily misalign the parts and damage the fork. If you go this way you may want to have a second fork printed in case you damage the first.
<br>


<br>
<br>
Press the two flanged tail shaft bearing into the tail case.
Then insert the tail boom and push it as far as possible without pressing against the tail belt rollers. <br>
Then bring the tail belt out the bottom from inside the tail case and insert the tail pulley. <br>
Push the tail pulley inside the tail case.
<br>


<br>
<br>
Once the tail case is pressed all the way in, use a 1.5mm drill bit to put a hole in the tail boom. Then use a 2.2x6 or similar screw to locate the tail case. <br>
Then use a 2mm pin and drive it through the tail pulley and the 2mm hole opened on the flat spot of the tail shaft.
<br>
<br>
Install the tail arm assembly with an M3x16 bolt. 
<br>
Use the printed tail dampers or the original ones to instal the tail spindle.
<br>
<br>



<br>
<br>
The tail grip links can be attached to the tail fork using 2mm pins or M2x12 and nut. In the case of the pin make sure the pin has enough resistance going into the nylon part to be stable under vibration but also not to prevent the tail form moving completely free. When using bolt and nut use thread lock and make sure the nut is not on tight to interfere with free movement.
<br>
The M2.5 that connect the grip links to the grips must be theaded in with care. Due to the printing process the parts may not be absolutely perfect and in this can produce some friction at high blade angles. Make sure you test this and if required keep the M2.5 bolt slightly loose. Test everything moves smoothly and freely.
<br>
Install the tail fin as shown.
<br>
<br>


<br>

</details>
<br>

## Servo Installation:
<details> 
<summary> Open Chapter </summary>
Servos are strighforward to install.
<br>
The ball link distance on all servos is 14mm.
<br>
<br>


<br>
<br>

### Following servo instllation, measure and cut the appropriate length of the tail rod.
</details> 
<br>

## Final Head Assembly and Grip Links:
<details> 
<summary> Open Chapter </summary>
The grip links require 30-35mm threaded rods. Use 2.5mm so that the grip link tubes work. If you use 3mm you have to design your own grip link tubes.

|Link | Ball link distance *| Center-to-center distance |
|---|---|---|
|Grip link | 16.5mm | 54mm |
|Swash link | 19mm | 57mm |
<br>
* with Mikado 2.5mm ball links.
<br>
<br>
Undamped head: No washers are used between the head and the grip bearings. If the grips have zero play when assembled onto the head, then adjust the internal washer in both grips so when everything is assembled there is a very small gap/play. The undapmed head may have oscillations at certain head speeds depending on the tightness of the head-grips assembly.
<br>
<br>
Damped head: Use washers between the head and the grip bearing (0.5mm). The head should not be tight and the grips should fall freely when all assembled.
<br>
Depending on the head you will use (damped or undamped) the gains and general setup of the the FBL can be very different. 
<br>
<br>


<br>
<br>


<br>
<br>

</details>
<br>

## Completing the assembly:
<details> 
<summary> Open Chapter </summary>
Install the ESC on the front tray. A specific tray for the HW 150 is provided. Other trays can be designed and printed (hole spacing on the carbon 42mm and frame width 44mm). If you design a tray for a specific ESC don;t forget to upload it to the repository (Other parts). 
<br>
The right side frame has slots for cable ties to pass through and hold the wire bunddle routed to the back of the heli.
<br>
<br>



<br>

### IMPORTANT: After each flight, especially the first few flights, thoughroughly check all screws, parts, linkages for any excessive wear or damage. Each build is unique, each printer produces somewhat different strength parts so treat your heli as a form of prototype and inspect it as one before you fly it.
<br>

</details>

<br>

## Canopy Assembly:
<details> 
<summary> Open Chapter </summary>
<br>
The canopy is printed in section sto facilitate printing on personnal FDM 3D printers. The main canopy and windshield pieces include a 2mm lip on the endges which will be welded. Use a soldering iron to melt the lip and weld the pieces together.
<br>
The main body of the canopy consists of 4 parts: <br>
  
- canopy front
- canopy rear
- windshield front
- windshield back
<br>
  
The recommended sequence of welding the pieces together is:<br>
  
  - front section of the canopy with the front section of the windshield
  - add the rear section of the windshield
  - add the rear section of the canopy

Cut the connecting material to free up the rear section of the canopy.
IMPORTANT: Depending on the layer adhesion you can achieve, the rear section of the canopy will have a varrying level of flexibility. Always be mindful of that and put the canopy on the heli when the blades are vertical to the body so the canopy doe not have to sterwetch much to clear the swash-grip links. See images at the end of this section.

<br>
Then there are the DS.2 lettering and the triangle which are printed as flat pieces and are then glued onto the canopy with CA glue.

<br>
Last are the two supports which are held in place by 2x 2.3mm screws for plastic for each support.









</details>
<br>

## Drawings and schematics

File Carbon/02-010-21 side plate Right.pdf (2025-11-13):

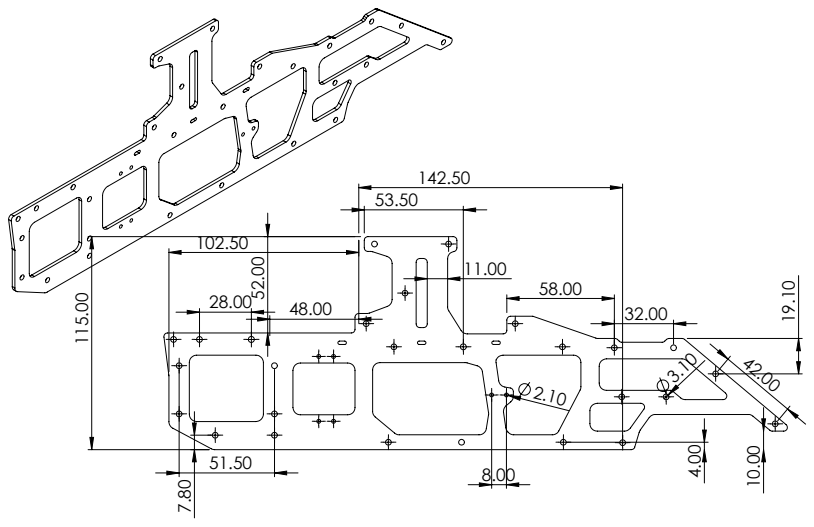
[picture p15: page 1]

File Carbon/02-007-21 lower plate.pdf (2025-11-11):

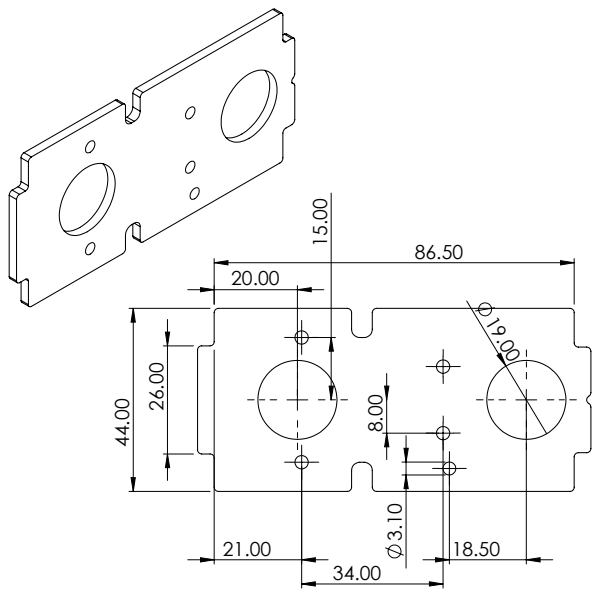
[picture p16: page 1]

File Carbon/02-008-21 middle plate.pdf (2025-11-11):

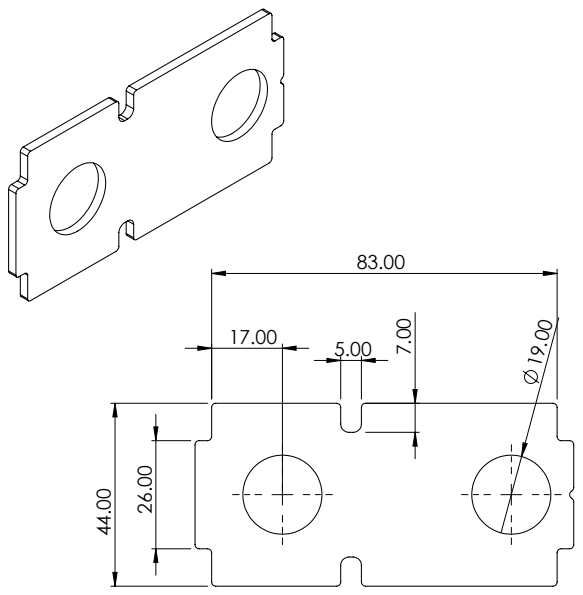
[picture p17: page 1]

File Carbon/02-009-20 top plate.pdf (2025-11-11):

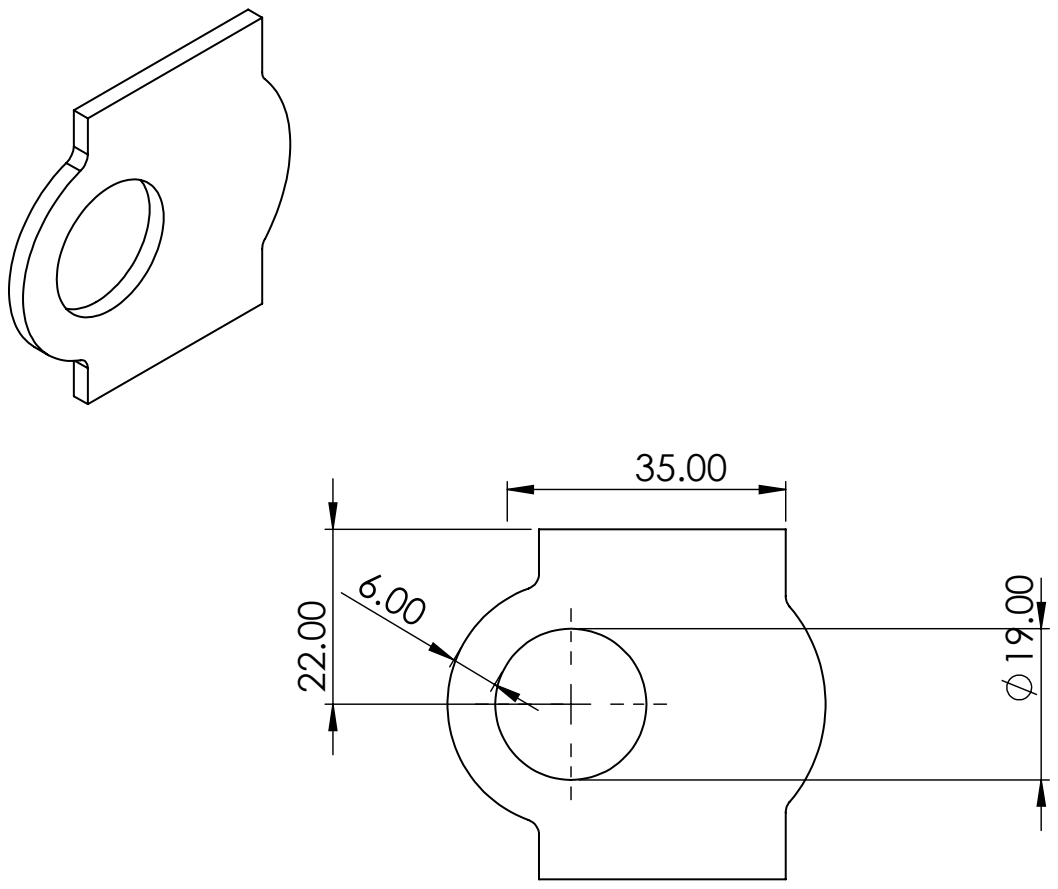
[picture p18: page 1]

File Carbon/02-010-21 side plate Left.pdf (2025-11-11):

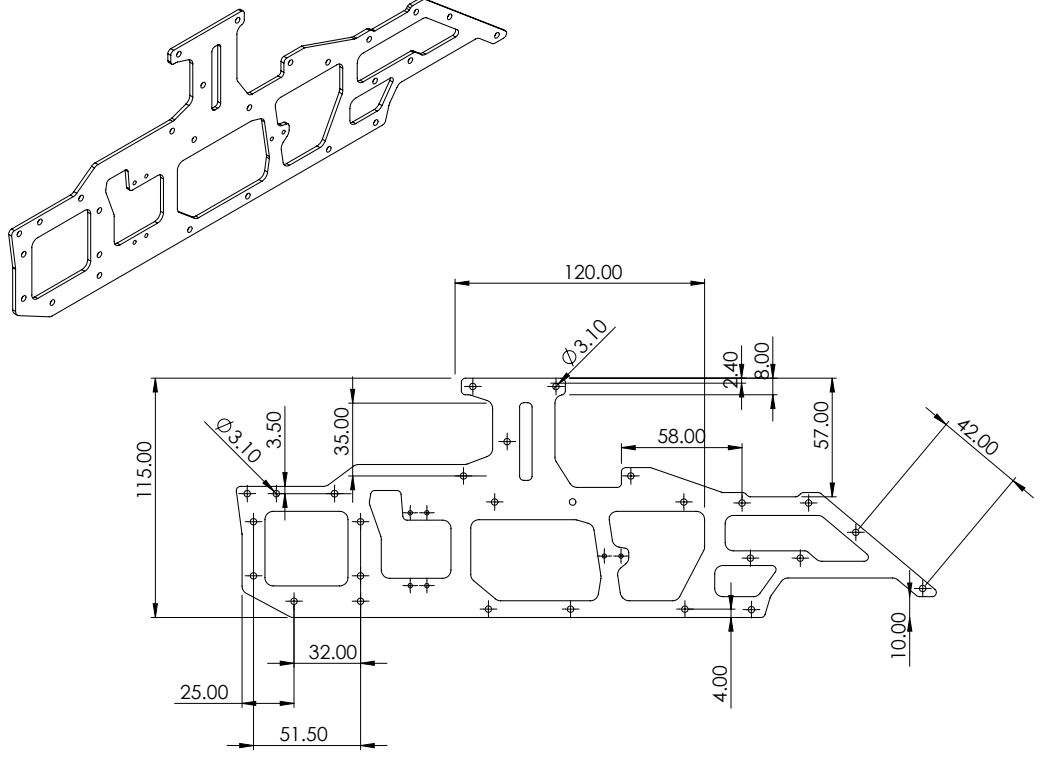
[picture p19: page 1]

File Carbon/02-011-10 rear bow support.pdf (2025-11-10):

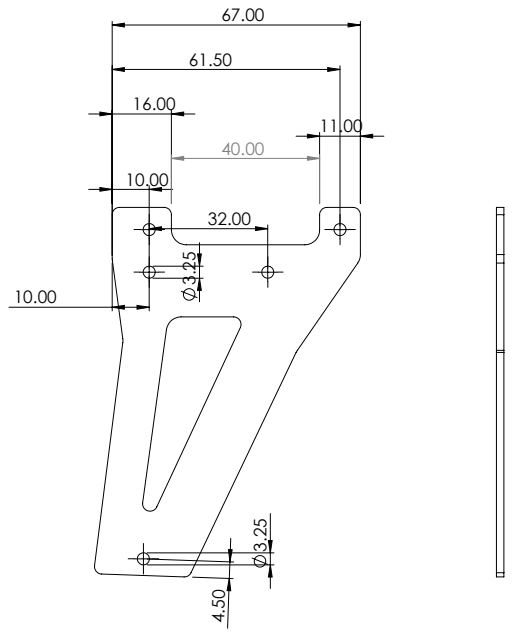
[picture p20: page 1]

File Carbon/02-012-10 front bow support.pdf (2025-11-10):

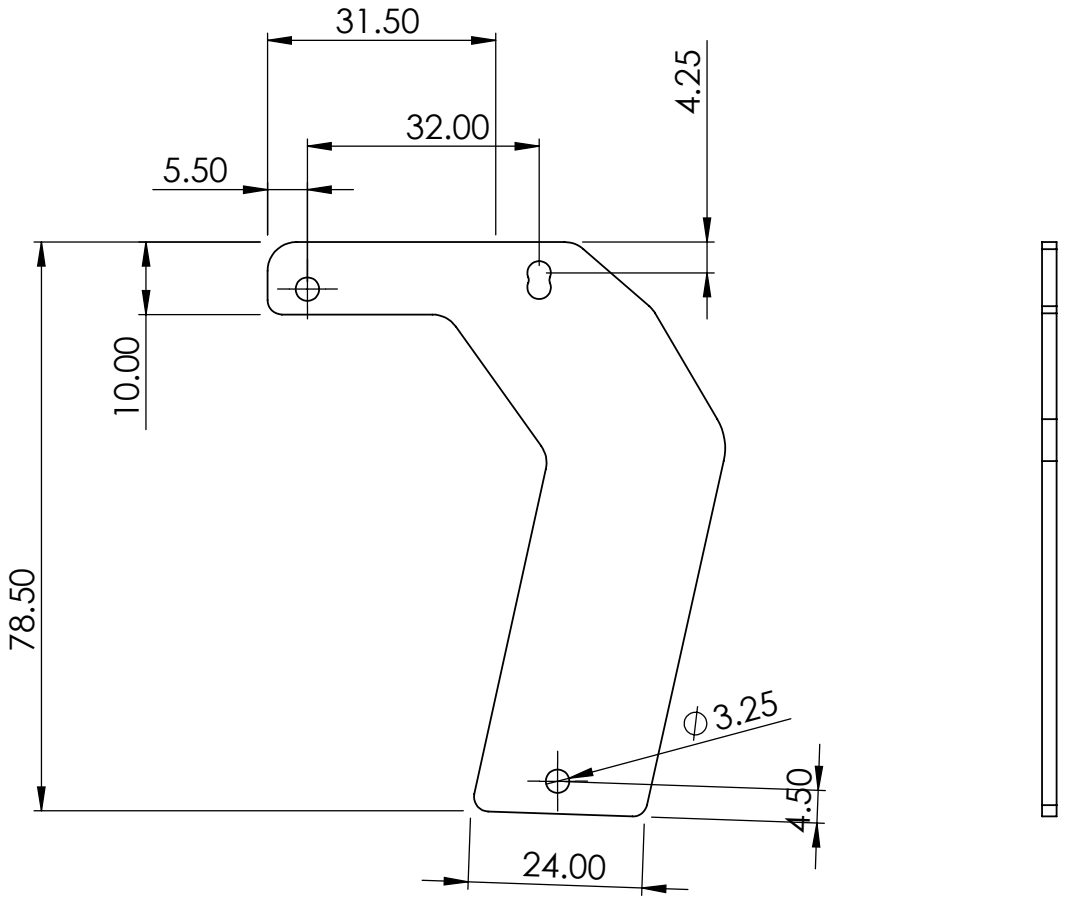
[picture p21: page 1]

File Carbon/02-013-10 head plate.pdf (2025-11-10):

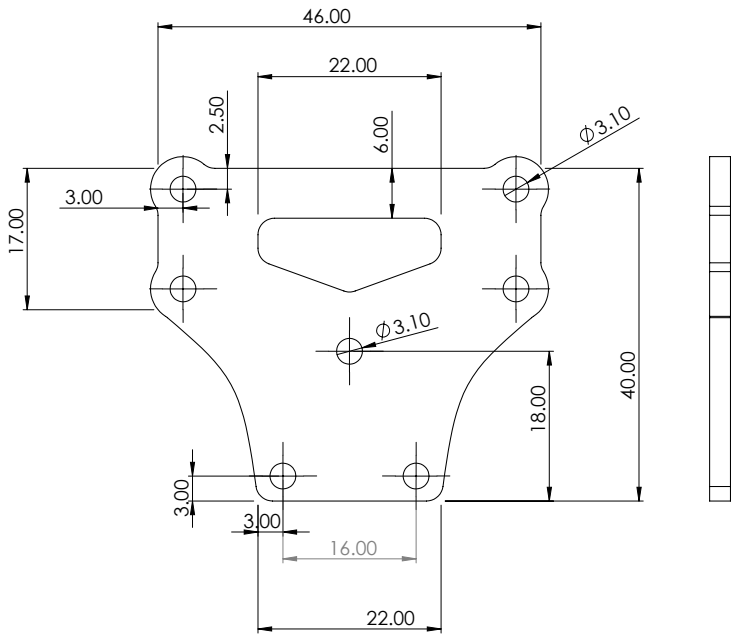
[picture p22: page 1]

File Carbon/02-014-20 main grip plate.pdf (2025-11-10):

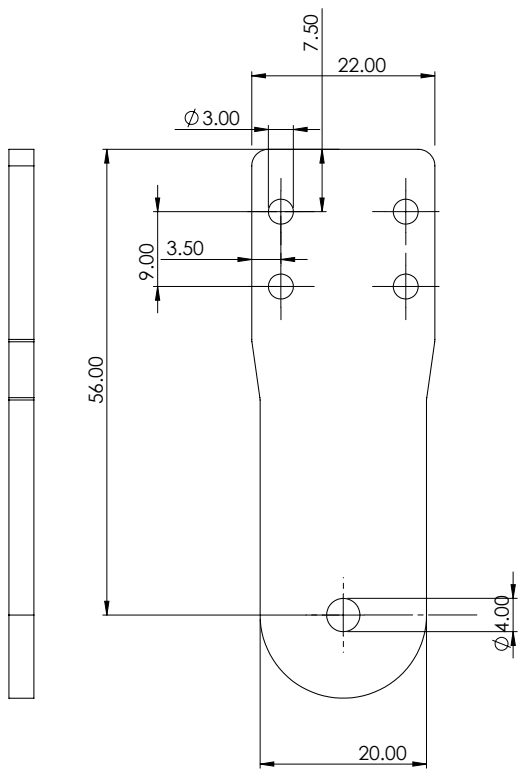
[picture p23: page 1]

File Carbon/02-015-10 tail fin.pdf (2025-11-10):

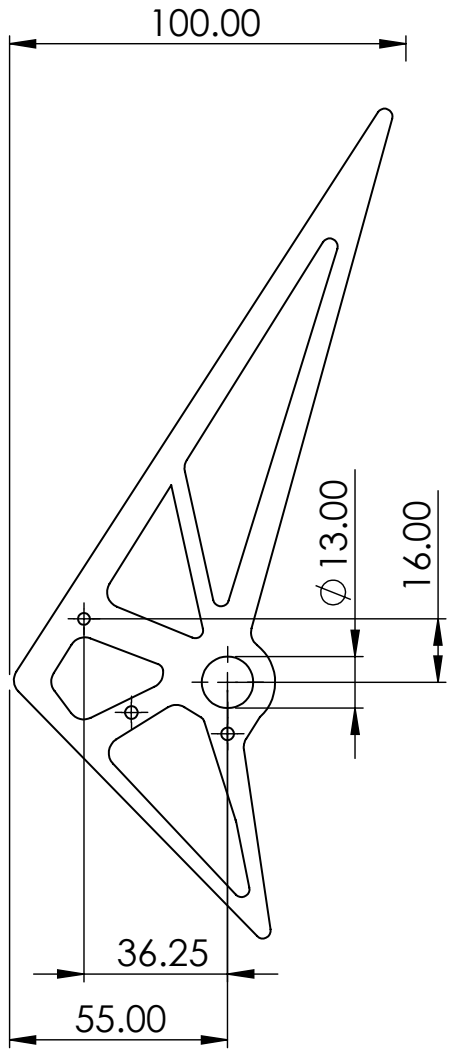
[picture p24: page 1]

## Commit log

2025-11-04 Rename DS2 front 0.9mm.STL to DS2 canopy front 0.9mm.STL
    [DS2 canopy front 0.9mm.STL]
2025-11-04 Rename DS2 rear 0.90mm.STL to DS2 canopy rear 0.90mm.STL
    [DS2 canopy rear 0.90mm.STL]
2025-11-04 Add build information for DS.2 RC helicopter
    Added general information about the DS.2 RC helicopter build, including required skills, materials, and tools.
2025-11-04 Enhance README with head assembly instructions
    Added detailed instructions for assembling damped and undamped heads, including preparation steps and required materials.
2025-11-04 Refine descriptions in README for clarity
    Updated descriptions for tail shaft and spindle, and one way bearing and hub.
